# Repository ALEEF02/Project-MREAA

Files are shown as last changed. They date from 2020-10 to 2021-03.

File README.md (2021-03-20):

# Project-MREAA

**M**otorized  
**R**otating  
**E**levation and  
**A**zimuth  
**A**ntenna  

I have just finished the build and am working on a guide! Stay tuned!

### Update July 10th, 2020
I am still working on this project, but 3 different people which I have asked to 3D print my main ring gear have fallen through (all for different reasons). I am currently working on getting my own 3D printer to print the part myself. Hopefully this project should be finished by August.

### Update October 2nd, 2020
Just about done! Need to print one more gear for the azimuth motor, which I've had to reprint multiple times due to mis-sizing on the internal hole. I am very behind schedule due to reopening of schools and my part-time job. Finished version should be (hopefully) published by month end. :D

### Update October 24th, 2020
I have finished the antenna! With this commit, I am uploading the code for the main and slave Arduinos as well as a setup test for the BNO055. Pictures, videos, parts list, and guide to come shortly!

### Update March 7th, 2021
With this update comes a preliminary guide with most of the critical information. It is *likely* I will add to it in the future.

# Full Guide

Here's a full instruction set on how to build your own antenna and how to wire it

## Parts
* 2x Arduino UNO
* 2x Stepper Motors
  * We used [these 2A motors](https://www.amazon.com/STEPPERONLINE-Stepper-Bipolar-Connector-compatible/dp/B00PNEQKC0)
* 2x Stepper Motor Drivers
  * We used [these 9-40V drivers](https://www.amazon.com/KNACRO-%E3%80%90Upgraded-Version%E3%80%91-Segments-Suitable/dp/B073NZBDNH)
* 1x Orientation device
  * Must have gyroscope and compass
  * We used the [BNO055 from Adafruit](https://www.adafruit.com/product/2472), which the code is written for
* Batteries to power the Stepper Motor Drivers
  * Must have enough voltage for both drivers
    * In our case, that's 2x9V = 18V
  * We used 3x [7.4V 610mAh LIPOs](https://www.amazon.com/610mAh-Battery-Hubsan-Quadcopter-Charging/dp/B082CVWS2W) we had lying around, wired in series
* Wiring
  * Jumper Wires
  * Longer Wire
    * Enough to where it can wrap several times while the antenna moves
	
#### Optional - the following can be changed to fit the needs of the build
*Ex: We modified the build afterwards to mount a camera for panorama shots*

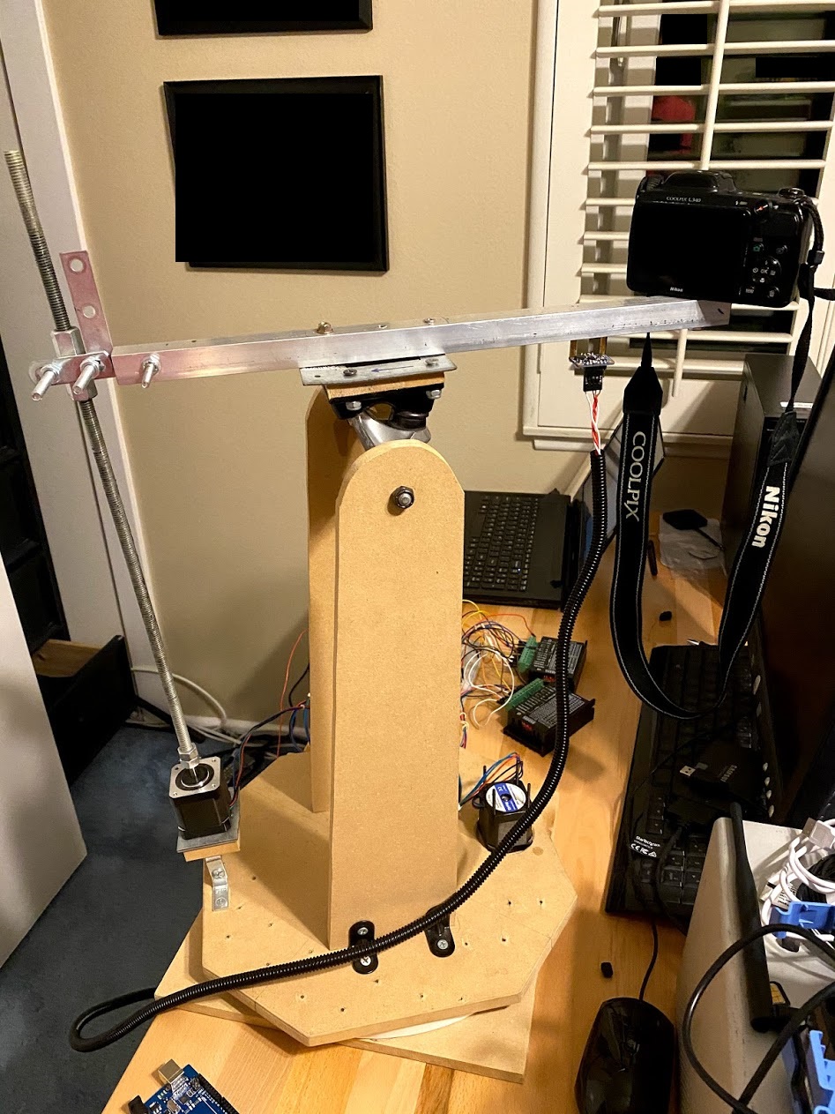
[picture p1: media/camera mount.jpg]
Camera Mount


* 3D printer (gears)
  * *Both gears are provided in .stl format and can be found [here](https://github.com/ALEEF02/Project-MREAA/tree/master/3D%20Models)*
* 1/2 inch aluminum square tube (boom)
* 3x copper pipes (director, driven element, and reflector)
  * Lengths depend on frequency of the antenna 
* U-bolts
* Sliding door wheels
    * Used to move the antenna on the base
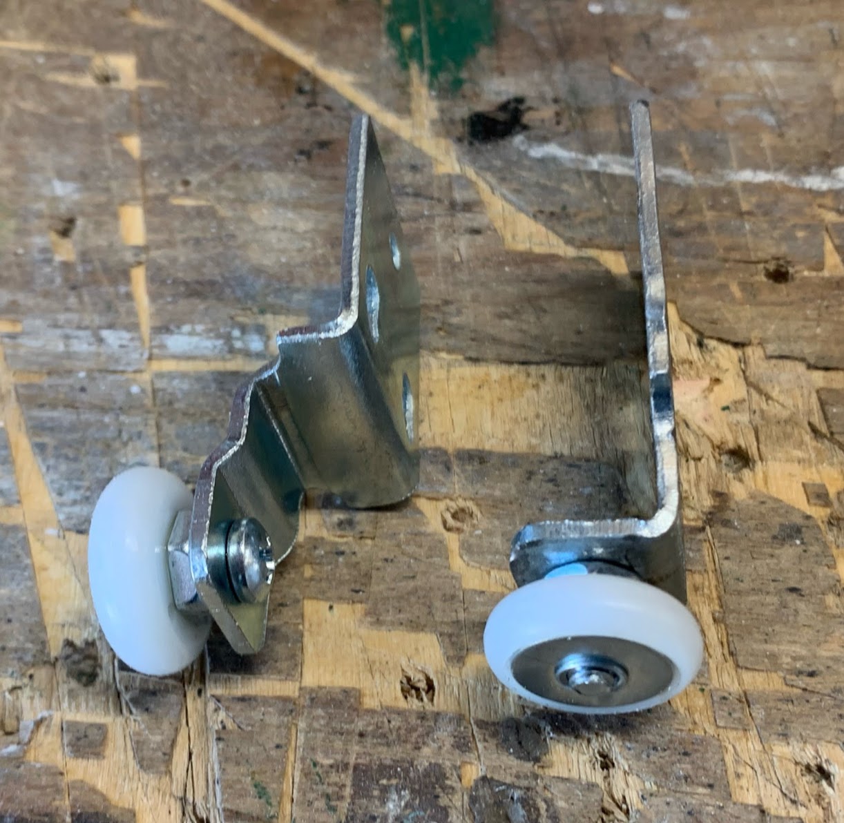
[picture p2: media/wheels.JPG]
Sliding Wheels
	
* Various other parts as needed...
	
## Steps

### Yagi Antenna
Our goal was to receive NOAA weather satellite signals at 137MHz. We sought to make a 3 element Yagi Uda antenna.

We began with rough calculations provided by [online calculators](https://www.changpuak.ch/electronics/yagi_uda_antenna_DL6WU.php). With these numbers we got a piece of 1/2 inch aluminum square tube as the boom. Three copper pipes (one director, one driven element, and one reflector), about 1/2 inch in diameter and cut to the specified lengths, were mounted to the boom at the calculated measurements.

Sliding Wheels
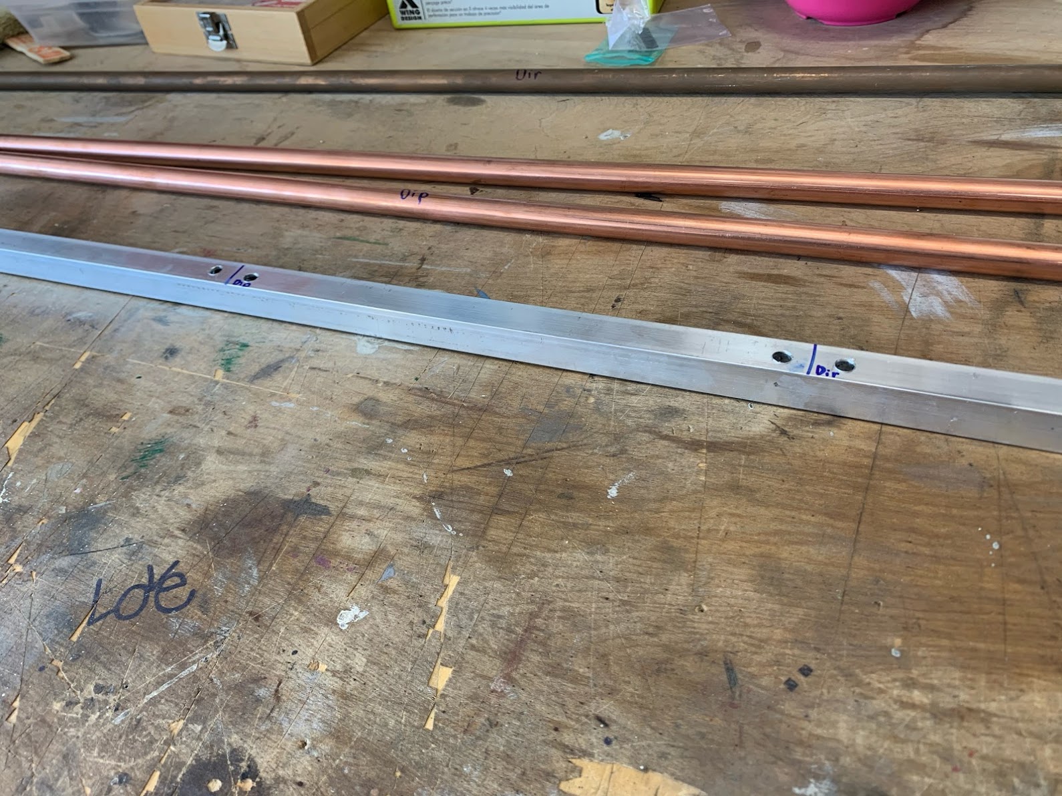
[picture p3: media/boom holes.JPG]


Mounting of the elements was done with U-bolts through the boom. The positive and negative leads were soldered to a length of coaxial cable and the joint was housed in a PVC junction box.

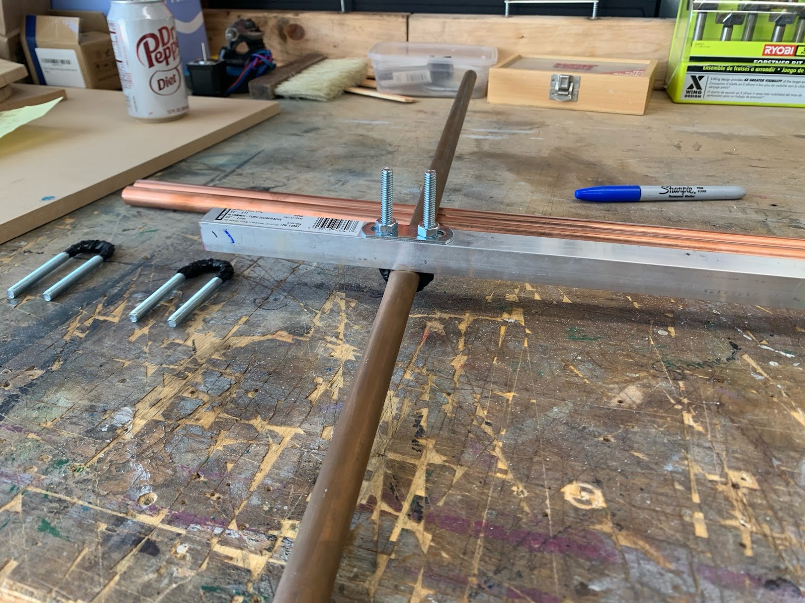
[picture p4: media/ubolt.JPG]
Using ubolts

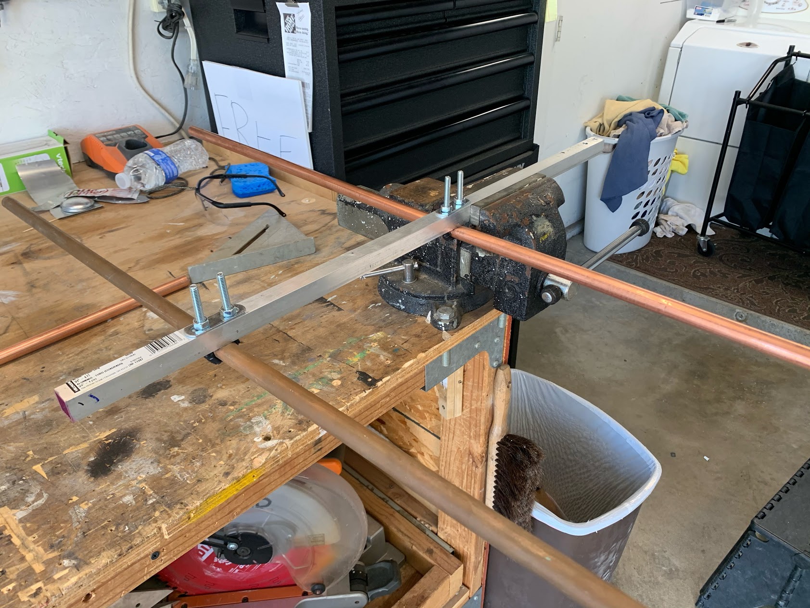
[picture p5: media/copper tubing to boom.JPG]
Attaching copper tubing to the boom

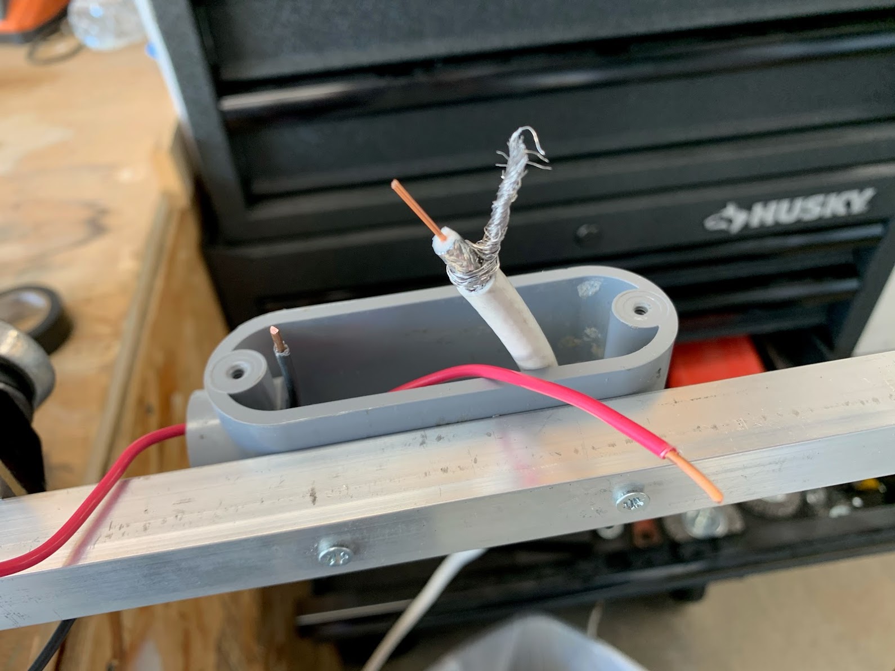
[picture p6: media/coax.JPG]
Coax Cabling

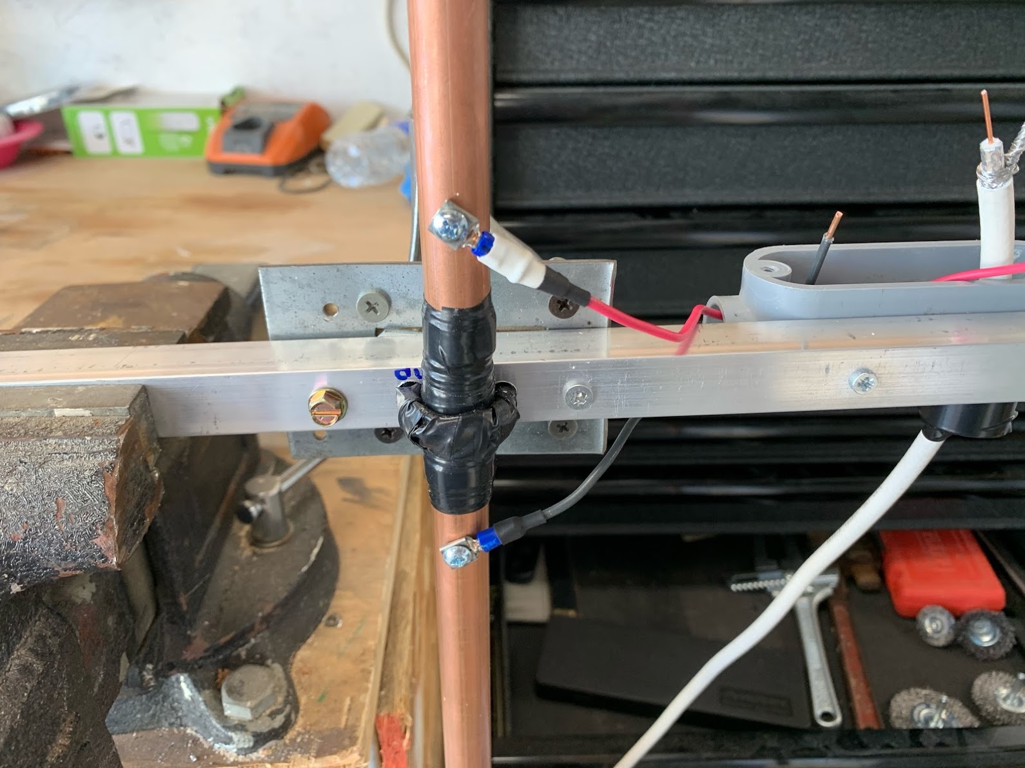
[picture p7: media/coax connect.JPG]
Coax cabling connected to the copper tubing


### Main Assembly
The whole antenna assembly was mounted on an old skateboard truck with the bearings pressed into two supports that held the antenna off the ground.

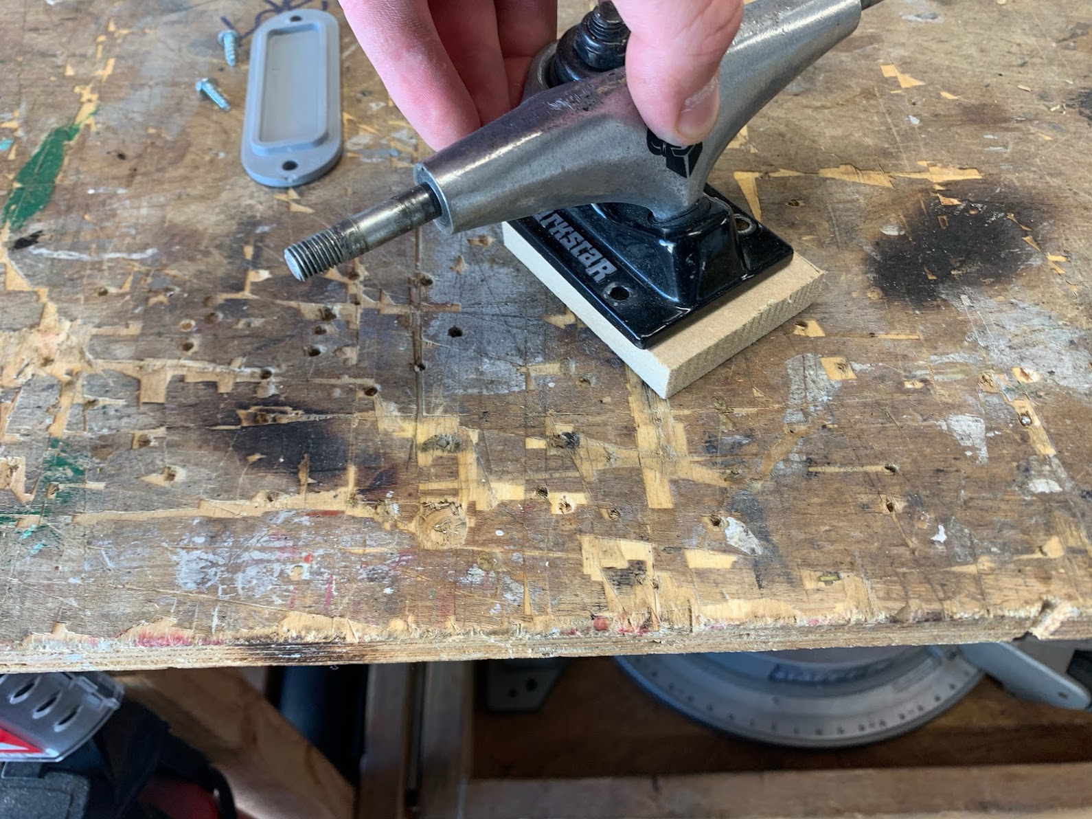
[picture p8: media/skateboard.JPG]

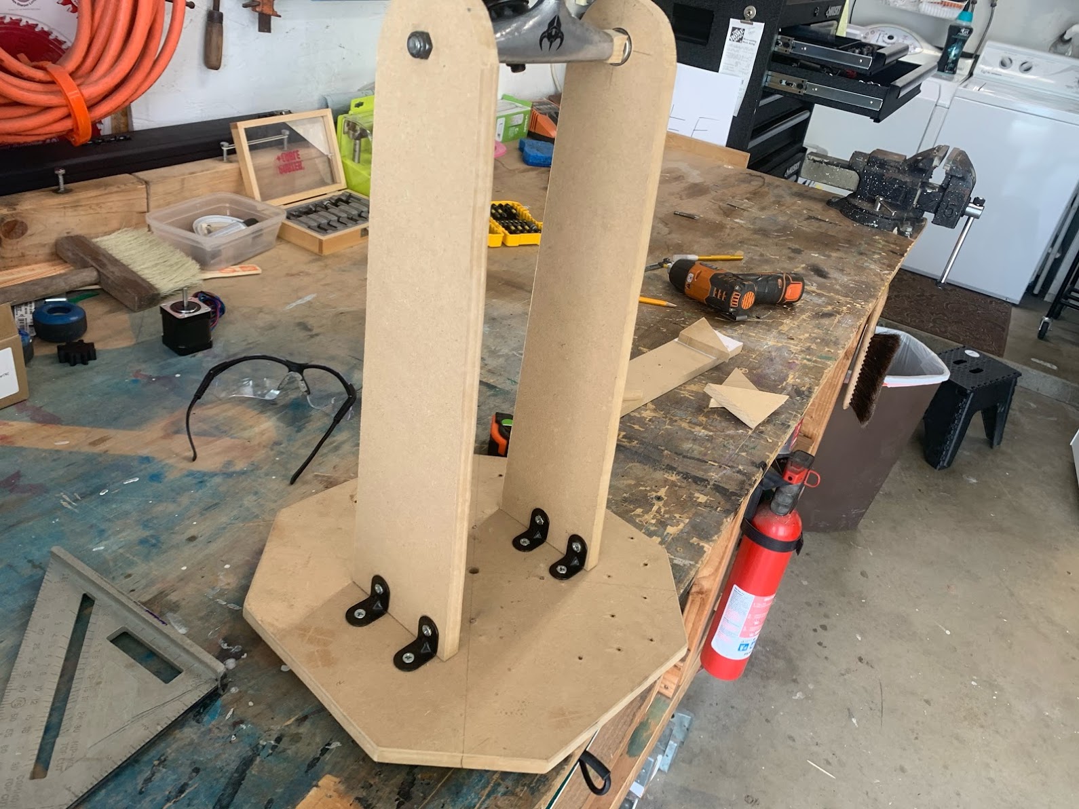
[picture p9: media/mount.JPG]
Full mounting solution


Vertical movement was accomplished by means of a screw that was allowed to change its angle to accommodate for the changing position of the stationary nut attached to the boom.

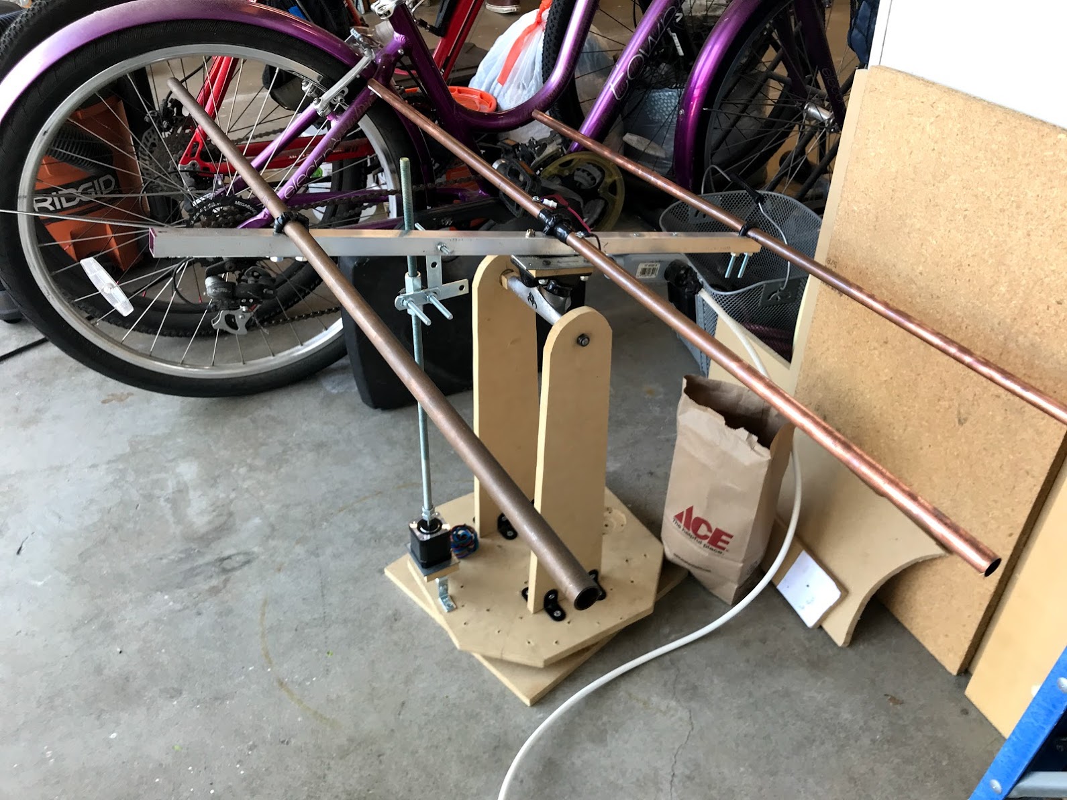
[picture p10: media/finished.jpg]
Finished, no wiring


### Wiring
Refer to the following diagram for wiring the antenna. A breadboard as displayed is not required, as you can solder the wires as well for a more permanent build.
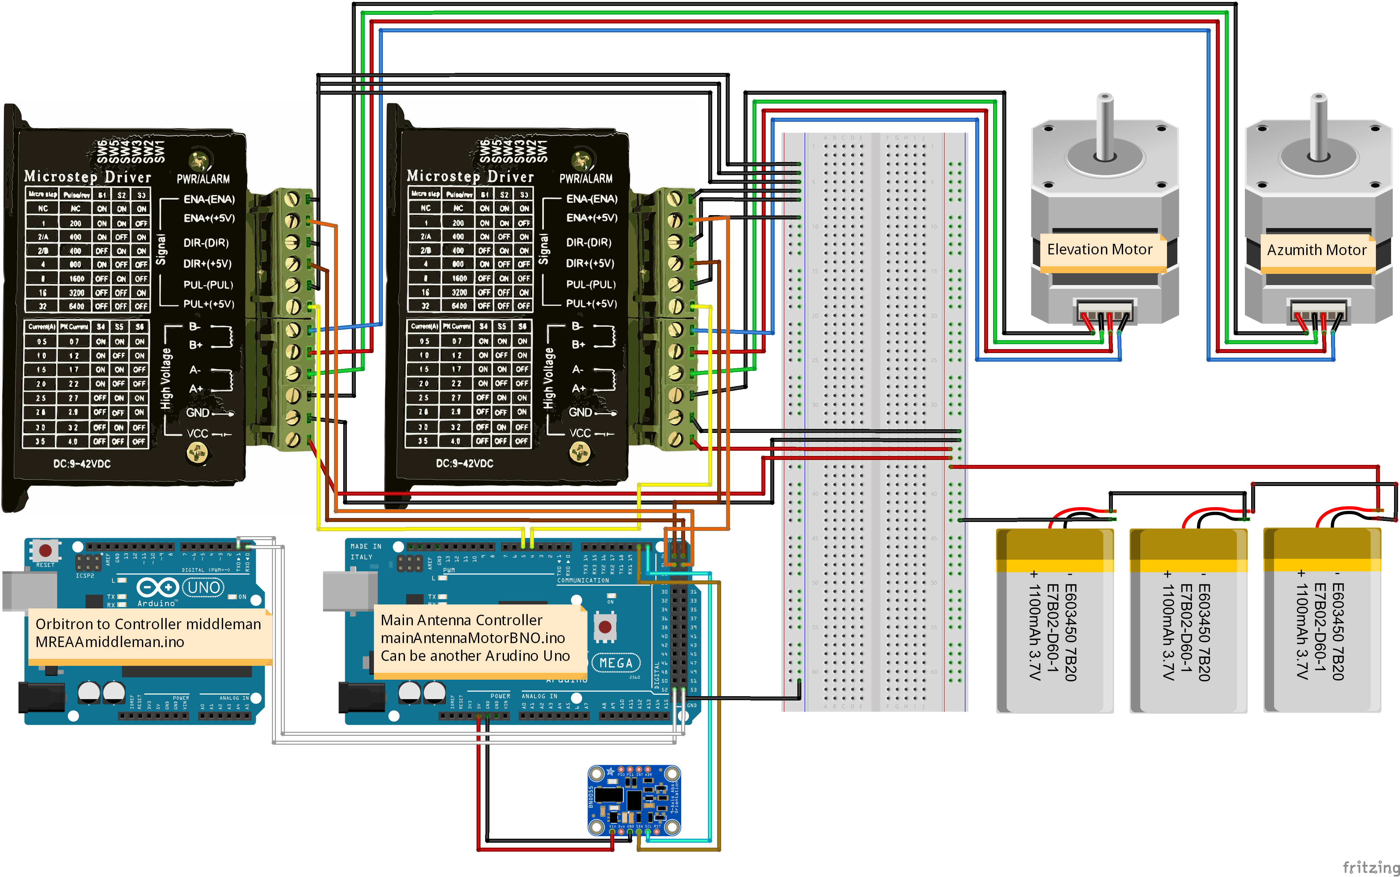
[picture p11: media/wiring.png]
Wiring Diagram


## Extra Photos and Videos
Early wiring and testing of the stepper motor using a compass

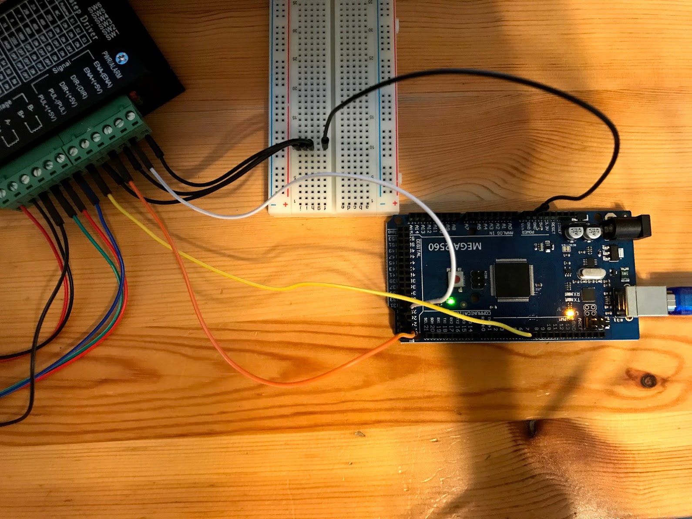
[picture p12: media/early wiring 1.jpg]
The beginnings


Using a compass (video)

First movement to the moon, October 24th, 2020 at 8:06 PM PDT
Movement to the Moon (video)

Tracking NOAA-18
Movement to NOAA-18

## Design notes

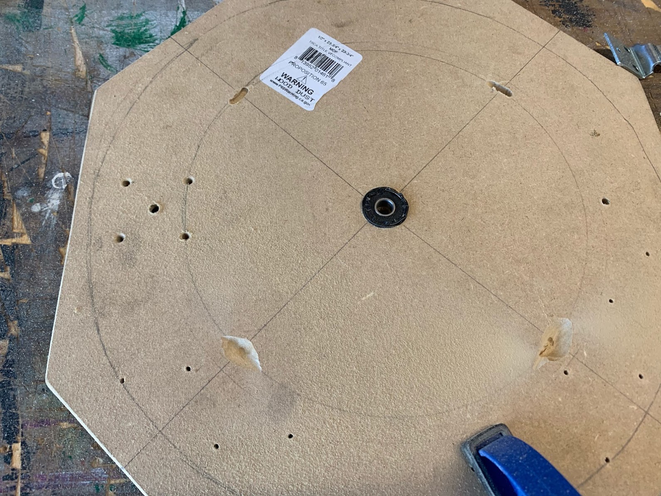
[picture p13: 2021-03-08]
media/base under.JPG

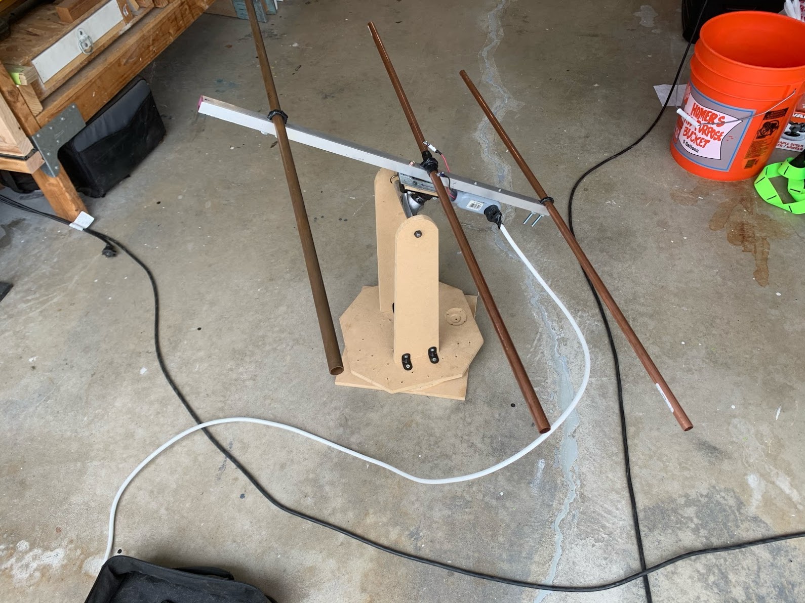
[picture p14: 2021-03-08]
media/completed no wire.JPG

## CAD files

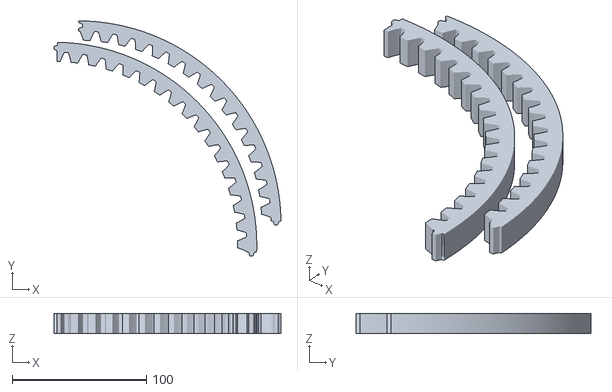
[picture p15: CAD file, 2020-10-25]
3D Models/REAL INTERNAL TR BL.stl
168.8 x 174.9 x 15.0

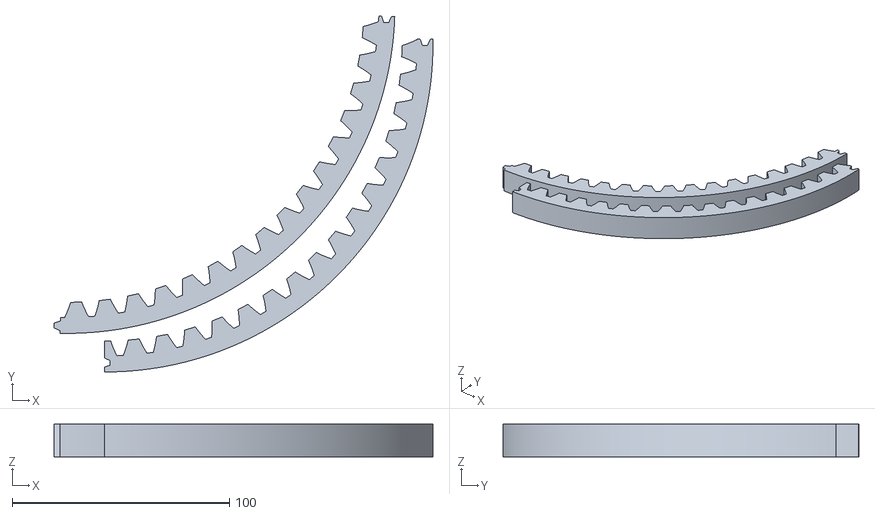
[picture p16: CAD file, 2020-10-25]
3D Models/REAL INTERNAL TL BR.stl
174.6 x 164.0 x 15.0

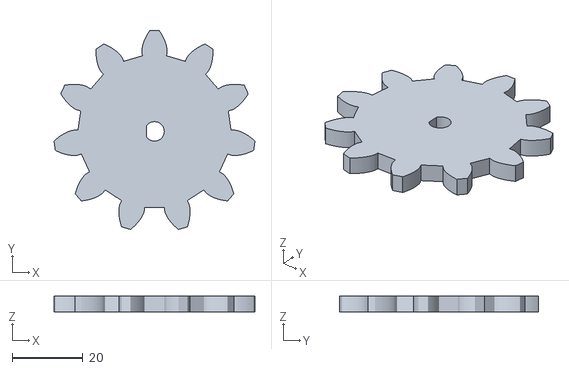
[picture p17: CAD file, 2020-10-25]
3D Models/spur 11 teeth 5.5_fixed.stl
56.9 x 56.3 x 4.50

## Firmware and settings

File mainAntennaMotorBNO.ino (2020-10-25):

// Main code to interact with Orbitron and move the motors into position. Uses BNO005

#include <SoftwareSerial.h>
#include <StringSplitter.h>
#include <Wire.h>
#include <Adafruit_Sensor.h>
#include <Adafruit_BNO055.h>
#include <utility/imumaths.h>
#include <WString.h>

// Setup secondary serial through a second Arduino for Orbitron communication
SoftwareSerial secondSer(53, 52);

uint16_t BNO055_SAMPLERATE_DELAY_MS = 100;
Adafruit_BNO055 bno = Adafruit_BNO055(55, 0x28);

const float Pi = 3.14159;

//Change the pins to match the pins you use. A = Azumith, E = Elevation
const int stepPinA = 5; 
const int dirPinA = 23; 
const int enPinA = 25;
const int stepPinE = 4; 
const int dirPinE = 22; 
const int enPinE = 24;

/* For LED
const int DI = 12;
const int RW = 11;
const int DB[] = {3, 4, 5, 6, 7, 8, 9, 10};// use array to select pin for bus
const int Enable = 2;
*/

double Mag_x, Mag_y, Mag_z, Mag_pitch, Mag_roll;      

double az = 0.0;
double el = 0.0; // Initial elevation and azumith
double heading = 0.0;
double elevation = 8.0;

// Toggle Motor Usage
boolean on = true;

/* LCD display
 *  
void LcdCommandWrite(int value) {
  // define all pins
  int i = 0;
  for (i=DB[0]; i <= DI; i++) // assign value for bus
    {
       digitalWrite(i,value & 01);// for 1602 LCD, it uses D7-D0( not D0-D7) for signal identification; here, it’s used for signal inversion. 
       value >>= 1;
    }
  digitalWrite(Enable,LOW);
  delayMicroseconds(1);
  digitalWrite(Enable,HIGH);
  delayMicroseconds(1);  // wait for 1ms
  digitalWrite(Enable,LOW);
  delayMicroseconds(1);  // wait for 1ms
}

void LcdDataWrite(int value) {
  // initialize all pins
  int i = 0;
  digitalWrite(DI, HIGH);
  digitalWrite(RW, LOW);
  for (i=DB[0]; i <= DB[7]; i++) {
       digitalWrite(i,value & 01);
       value >>= 1;
  }
  digitalWrite(Enable,LOW);
  delayMicroseconds(1);
  digitalWrite(Enable,HIGH);
  delayMicroseconds(1);
  digitalWrite(Enable,LOW);
  delayMicroseconds(1);  // wait for 1ms
}

void writeToLCD(String input) {
  LcdCommandWrite(0x01);  // clear the screen, cursor position returns to 0  
  delay(10); 
  LcdCommandWrite(0x80); 
  delay(10);
  int inLength = input.length();

  char charArray[inLength];
  strcpy(charArray, input.c_str());
  int i = 0;
  for (i = 0; i < inLength; i++) {
    if (i == 15) {
      delay(10);
      LcdCommandWrite(0xc0);  // set cursor position at second line, second position
      delay(10); 
    }
    LcdDataWrite(charArray[i]);
  }
}
*/

void displayCalStatus(void)
{
  /* Get the four calibration values (0..3) */
  /* Any sensor data reporting 0 should be ignored, */
  /* 3 means 'fully calibrated" */
  uint8_t system, gyro, accel, mag;
  system = gyro = accel = mag = 0;
  bno.getCalibration(&system, &gyro, &accel, &mag);
 
  /* The data should be ignored until the system calibration is > 0 */
  Serial.print("\t");
  if (!system)
  {
    Serial.print("! ");
  }
 
  /* Display the individual values */
  Serial.print("Sys:");
  Serial.print(system, DEC);
  Serial.print(" G:");
  Serial.print(gyro, DEC);
  Serial.print(" A:");
  Serial.print(accel, DEC);
  Serial.print(" M:");
  Serial.println(mag, DEC);
}

void checkGoodCal(void) {
  adafruit_bno055_offsets_t offsets;
  uint8_t system, gyro, accel, mag;
  system = gyro = accel = mag = 0;
  bno.getCalibration(&system, &gyro, &accel, &mag);
  if (system == 3 && gyro == 3 && mag == 3) {
    bno.getSensorOffsets(offsets);
    Serial.print("Good Calibration: ");
    Serial.print(offsets.mag_offset_x);
    Serial.print("\t");
    Serial.print(offsets.mag_offset_y);
    Serial.print("\t");
    Serial.println(offsets.mag_offset_z);
  }
}

void getHeading() {
  sensors_event_t orientationData, magnetometerData;
  bno.getEvent(&orientationData, Adafruit_BNO055::VECTOR_EULER);
  bno.getEvent(&magnetometerData, Adafruit_BNO055::VECTOR_MAGNETOMETER);
  Mag_x = magnetometerData.magnetic.x;
  Mag_y = magnetometerData.magnetic.y;
  Mag_z = magnetometerData.magnetic.z;
  Mag_pitch = orientationData.orientation.y * DEG_TO_RAD;
  Mag_roll = orientationData.orientation.z * DEG_TO_RAD;
  Mag_x = Mag_x * cos(Mag_pitch) + Mag_y * sin(Mag_roll) * sin(Mag_pitch) - Mag_z * cos(Mag_roll) * sin(Mag_pitch);
  Mag_y = Mag_y * cos(Mag_roll) + Mag_z * sin(Mag_roll);
  heading = (atan2(Mag_y, Mag_x) * 180) / Pi;
  heading += 11.6;
  heading += 180;
  if (heading >= 360) {
    heading -= 360;
  }
}

void getElevation() {
  sensors_event_t orientationData;
  bno.getEvent(&orientationData, Adafruit_BNO055::VECTOR_EULER);
  elevation = double(-orientationData.orientation.y);
}

void displayInfo() {
  Serial.print("Sat AZ: ");
  Serial.print(az);
  Serial.print("  El: ");
  Serial.println(el);
  Serial.print("Ant AZ: ");
  Serial.print(heading);
  Serial.print("  El: ");
  Serial.println(elevation);
  Serial.println();
  
  /* LCD Display
  
  String displayText = "sAZ:";
  displayText += String(az);
  displayText += "EL:";
  displayText += String(el);
  writeToLCD(displayText);*/
}

void setup(void)
{
  pinMode(LED_BUILTIN, OUTPUT);
  Wire.begin();
  Serial.begin(115200);
  while(!Serial){};
  delay(100);

  digitalWrite(LED_BUILTIN, HIGH);
  Serial.println("Starting Project MREAA...");
  Serial.println();

  if (!bno.begin())
  {
    /* There was a problem detecting the BNO055 ... check your connections */
    Serial.print("Ooops, no BNO055 detected ... Check your wiring or I2C ADDR!");
    while (1);
  }

  delay(1000);

  // Start connection to Arduino UNO board for Orbitron communitcation
  secondSer.begin(9600);
  secondSer.setTimeout(50);

  // Sets the two pins as Outputs
  pinMode(stepPinA,OUTPUT); 
  pinMode(dirPinA,OUTPUT);
  pinMode(enPinA,OUTPUT);
  pinMode(stepPinE,OUTPUT); 
  pinMode(dirPinE,OUTPUT);
  pinMode(enPinE,OUTPUT);
  digitalWrite(enPinA,LOW);
  digitalWrite(enPinE,LOW);
  
  getHeading();
  getElevation();

  //while(secondSer.available() <= 0);

  /* For LCD
  int i = 0;
  for (i=Enable; i <= DI; i++) {
     pinMode(i,OUTPUT);
  }
  delay(100);  // initialize LCD after a brief pause for LCD control
  LcdCommandWrite(0x38);  // select as 8-bit interface, 2-line display, 5x7 character size 
  delay(64);                      
  LcdCommandWrite(0x38);  // select as 8-bit interface, 2-line display, 5x7 character size 
  delay(50);                      
  LcdCommandWrite(0x38);  // select as 8-bit interface, 2-line display, 5x7 character size             
  delay(20);                      
  LcdCommandWrite(0x06);  // set input mode, auto-increment, no display of shifting
  delay(20);                      
  LcdCommandWrite(0x0E);  // display setup,turn on the monitor, cursor on, no flickering
  delay(20);                      
  LcdCommandWrite(0x01);  // clear the screen, cursor position returns to 0
  delay(100);                      
  LcdCommandWrite(0x80);  //  display setup, turn on the monitor, cursor on, no flickering
  
  delay(20);
  writeToLCD("SerialAvalible");*/
}

/*void processIncomingByte (const byte inByte)
{
  static unsigned int input_pos = 0;

  switch (inByte) {
    case '\n':   // end of text
      incString [input_pos] = 0;  // terminating null byte
       // reset buffer for next time
      input_pos = 0;  
      break;
    case '\r':   // discard carriage return
      break;
    default:
      // keep adding if not full ... allow for terminating null byte
      if (input_pos < (11))
        incString [input_pos++] = inByte;
      break;
   }
}*/


char incString[11];
int byteNum = 0;
char terminate = '\n';
char item[6];

void loop(void)
{
  secondSer.listen();
  if (secondSer.available() > 6) {   
    // Use a C String to prevent the fragmentation of the heap
    memset(incString, 0, sizeof incString);
    memset(item, 0, sizeof item);
    byteNum = 0;
    
    // Read the incoming bytes
    Serial.println("Second serial avalible");
    while(secondSer.available() > 0) {
      char inC = secondSer.read();
      if (inC != terminate) {
        incString[byteNum] = inC;
      } else {
        incString[byteNum] = '\0';
        break;
      }
      byteNum++;
    }
    
    Serial.print("Got Message: ");
    Serial.println(incString);

    StringSplitter *splitter = new StringSplitter(incString, ';', 2);
    
    for(int i = 0; i < 2; i++){
      item[5] = '\0';
      strcpy(item, splitter->getItemAtIndex(i).c_str());
      if (i == 0) {
        az = atof(item);
      } else {
        el = atof(item);
      }
    }

    //Free the splitter pointer. Fixes a large memory leak. I am aware there is also another memory leak and I am looking into it
    free(splitter);
    getHeading();
    getElevation();
    displayInfo();
    delay(10);
  } else {
    getHeading();
    getElevation();
    displayInfo();
  }
  
  if (on == true) {
    
    // Check and move to elevation
    if (!(elevation - el < 5 && elevation - el > -5) && (el > 5 && el < 70)) {
      int spinCT = 0;
      int speedMotor = 10000;
      if (elevation - el < -5) {
        digitalWrite(dirPinE,HIGH);
        Serial.println("Moving up...");
        while (elevation - el < -5 && el < 70) {
          Serial.println("Elevation: " + String(elevation) + ", Dest: " + String(el));
          for (int i = 0; i < 200; i++) {
            digitalWrite(stepPinE,HIGH); 
            delayMicroseconds(speedMotor); 
            digitalWrite(stepPinE,LOW); 
            delayMicroseconds(speedMotor);
          }
          spinCT++;
          Serial.println("Getting elevation...");
          getElevation();
          displayInfo();
          
          if (spinCT == 2) {
            Serial.println("Speeding up...");
            speedMotor = 5000;
          }
          if (spinCT == 4) {
            Serial.println("Speeding up again...");
            speedMotor = 2500;
          }
        }
      } else {
        digitalWrite(dirPinE,LOW);
        Serial.println("Moving down...");
        while (elevation - el > 5 && el > 5) {
          Serial.println("Elevation: " + String(elevation) + ", Dest: " + String(el));
          for (int i = 0; i < 200; i++) {
            digitalWrite(stepPinE,HIGH); 
            delayMicroseconds(speedMotor); 
            digitalWrite(stepPinE,LOW); 
            delayMicroseconds(speedMotor);
          }
          spinCT++;
          Serial.println("Getting elevation...");
          getElevation();
          displayInfo();
          
          if (spinCT == 2) {
            Serial.println("Speeding up...");
            speedMotor = 5000;
          }
          if (spinCT == 4) {
            Serial.println("Speeding up again...");
            speedMotor = 2500;
          }
        }
      }
    }
  
  
    // Check and move to azumith
    if (!((heading - az < 5 && heading - az > -5) || (heading - az > 355 || heading - az < -355)) && el > 5) {
      int spinCT = 0;
      int speedMotor = 80000;
      if ((heading - az < -5 && heading - az > -180) || (heading - 360 - az > -180)) {
        digitalWrite(dirPinA,HIGH); // CLOCKWISE!
        Serial.println("Moving clockwise...");
        while (heading - az < -5 || (heading - az < 355 && heading - az > 180)) {
          Serial.println("Heading: " + String(heading) + ", Dest: " + String(az));
          for (int i = 0; i < 14; i++) {
            digitalWrite(stepPinA,HIGH); 
            delayMicroseconds(speedMotor); 
            digitalWrite(stepPinA,LOW); 
            delayMicroseconds(speedMotor);
          }
          spinCT++;
          Serial.println("Getting heading...");
          getHeading();
          displayInfo();
          if (spinCT == 6) {
            Serial.println("Speeding up...");
            speedMotor = 40000;
          }
        }
      } else {
        digitalWrite(dirPinA,LOW); // COUNTER-CLOCKWISE!
        Serial.println("Moving counterclockwise...");
        while (heading - az > 5  || (heading - az > -355 && heading - az < -180)) {
          Serial.println("Heading: " + String(heading) + ", Dest: " + String(az));
          for (int i = 0; i < 14; i++) {
            digitalWrite(stepPinA,HIGH); 
            delayMicroseconds(speedMotor); 
            digitalWrite(stepPinA,LOW); 
            delayMicroseconds(speedMotor);
          }
          spinCT++;
          Serial.println("Getting heading...");
          getHeading();
          displayInfo();
          if (spinCT == 6) {
            Serial.println("Speeding up...");
            speedMotor = 40000;
          }
        }
      }
    }

  }

  delay(1000);
}

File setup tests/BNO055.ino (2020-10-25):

// Tests the BNO055

#include <Wire.h>
#include <Adafruit_Sensor.h>
#include <Adafruit_BNO055.h>
#include <utility/imumaths.h>

/* This driver uses the Adafruit unified sensor library (Adafruit_Sensor),
   which provides a common 'type' for sensor data and some helper functions.

   To use this driver you will also need to download the Adafruit_Sensor
   library and include it in your libraries folder.

   You should also assign a unique ID to this sensor for use with
   the Adafruit Sensor API so that you can identify this particular
   sensor in any data logs, etc.  To assign a unique ID, simply
   provide an appropriate value in the constructor below (12345
   is used by default in this example).

   Connections
   ===========
   Connect SCL to analog 5
   Connect SDA to analog 4
   Connect VDD to 3.3-5V DC
   Connect GROUND to common ground

   History
   =======
   2015/MAR/03  - First release (KTOWN)
*/

/* Set the delay between fresh samples */
uint16_t BNO055_SAMPLERATE_DELAY_MS = 100;

// Check I2C device address and correct line below (by default address is 0x29 or 0x28)
//                                   id, address
Adafruit_BNO055 bno = Adafruit_BNO055(55, 0x28);

void setup(void)
{
  Serial.begin(115200);
  Serial.println("Orientation Sensor Test"); Serial.println("");

  /* Initialise the sensor */
  if (!bno.begin())
  {
    /* There was a problem detecting the BNO055 ... check your connections */
    Serial.print("Ooops, no BNO055 detected ... Check your wiring or I2C ADDR!");
    while (1);
  }

  delay(1000);
}

void loop(void)
{
  //could add VECTOR_ACCELEROMETER, VECTOR_MAGNETOMETER,VECTOR_GRAVITY...
  sensors_event_t orientationData , angVelocityData , linearAccelData, magnetometerData, accelerometerData, gravityData;
  bno.getEvent(&orientationData, Adafruit_BNO055::VECTOR_EULER);
  bno.getEvent(&angVelocityData, Adafruit_BNO055::VECTOR_GYROSCOPE);
  bno.getEvent(&linearAccelData, Adafruit_BNO055::VECTOR_LINEARACCEL);
  bno.getEvent(&magnetometerData, Adafruit_BNO055::VECTOR_MAGNETOMETER);
  bno.getEvent(&accelerometerData, Adafruit_BNO055::VECTOR_ACCELEROMETER);
  bno.getEvent(&gravityData, Adafruit_BNO055::VECTOR_GRAVITY);

  printEvent(&orientationData);
  printEvent(&angVelocityData);
  printEvent(&linearAccelData);
  printEvent(&magnetometerData);
  printEvent(&accelerometerData);
  printEvent(&gravityData);

  int8_t boardTemp = bno.getTemp();
  Serial.println();
  Serial.print(F("temperature: "));
  Serial.println(boardTemp);

  uint8_t system, gyro, accel, mag = 0;
  bno.getCalibration(&system, &gyro, &accel, &mag);
  Serial.println();
  Serial.print("Calibration: Sys=");
  Serial.print(system);
  Serial.print(" Gyro=");
  Serial.print(gyro);
  Serial.print(" Accel=");
  Serial.print(accel);
  Serial.print(" Mag=");
  Serial.println(mag);

  Serial.println("--");
  delay(BNO055_SAMPLERATE_DELAY_MS);
}

void printEvent(sensors_event_t* event) {
  double x = -1000000, y = -1000000 , z = -1000000; //dumb values, easy to spot problem
  if (event->type == SENSOR_TYPE_ACCELEROMETER) {
    Serial.print("Accl:");
    x = event->acceleration.x;
    y = event->acceleration.y;
    z = event->acceleration.z;
  }
  else if (event->type == SENSOR_TYPE_ORIENTATION) {
    Serial.print("Orient:");
    x = event->orientation.x;
    y = event->orientation.y;
    z = event->orientation.z;
  }
  else if (event->type == SENSOR_TYPE_MAGNETIC_FIELD) {
    Serial.print("Mag:");
    x = event->magnetic.x;
    y = event->magnetic.y;
    z = event->magnetic.z;
  }
  else if (event->type == SENSOR_TYPE_GYROSCOPE) {
    Serial.print("Gyro:");
    x = event->gyro.x;
    y = event->gyro.y;
    z = event->gyro.z;
  }
  else if (event->type == SENSOR_TYPE_ROTATION_VECTOR) {
    Serial.print("Rot:");
    x = event->gyro.x;
    y = event->gyro.y;
    z = event->gyro.z;
  }
  else if (event->type == SENSOR_TYPE_LINEAR_ACCELERATION) {
    Serial.print("Linear:");
    x = event->acceleration.x;
    y = event->acceleration.y;
    z = event->acceleration.z;
  }
  else {
    Serial.print("Unk:");
  }

  Serial.print("\tx= ");
  Serial.print(x);
  Serial.print(" |\ty= ");
  Serial.print(y);
  Serial.print(" |\tz= ");
  Serial.println(z);
}

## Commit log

2020-04-16 Add Adafruit compass and stepper motor test files
2020-04-28 Add gyro and I2C test files. Add libraries
2020-10-25 Add final code for main and slave Arduinos
2020-10-25 Add the 3D printable gears
    [REAL INTERNAL TL BR.stl, REAL INTERNAL TR BL.stl, spur 11 teeth 5.5_fixed.stl]
2021-03-20 Fix camera mount photo being inline
